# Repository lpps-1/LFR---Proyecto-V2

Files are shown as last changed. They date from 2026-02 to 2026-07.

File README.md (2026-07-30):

<div align="center">

[Linktree](https://linktr.ee/team.lpps1) | [GitHub](https://github.com/lpps-1) | **Status: Competition Ready**

</div>

---

## Team LPPS Overview

> **Team LPPS**, an elite youth-led competitive robotics and engineering collective based in Pakistan. Completely self-funded and operating independently with zero corporate or institutional backing, our core members peak at just 15 years old, yet we consistently dominate university-level national arenas, securing over 9 major championship titles. We are renowned for pushing the boundaries of indigenous hardware innovation, having pioneered Pakistan's first locally manufactured high-grip silicone wheels for competitive robotics. We are also currently working on Pakistan's first custom high-amp motor drivers and 16-channel sensors capable of a 1MHz sample rate, alongside advanced autonomous firmware architectures, custom onboard OLED control systems, and high-performance line-following robotics engineered for premier platforms such as the National Engineering Robotics Contest (NERC) at NUST EME.

### 1 - Introduction:
Hi! Line Follower Robot - Proyecto V2, is the second version of my line follower. The old one had some design flaws which I had solved in this design. So what I have made is a LFR with four TT motors for movement which will be paired with soft rubber tyre for extra traction as line followers need traction. Im using arduino nano for all the main processing, TB6612FNG as the motor driver for controlling the motors. What I have improved is that I have added a a 5 Channel TCRT5000 Array at the very front, which will be primarily detecting the line behind are two individual TCRT5000 Sensors on both sides that will be mainly used for detecting intersections and will also assist with turns. Two LEDs are also added that will turn on when the respective turn is being executed this will help in debugging and during a competition if the wrong LED turns on Ill know it will go off course and Ill be able to take the retry earlier instead of wasting time waiting for the robot to go off track. Lastly Im using a custom OS on the OLED which will show a starting animation which is also skippable then it will show multiple menu options. I have been working on it for about 4 months and its about to be completed but due to my upcoming final exams I have to delay it. The menu options will compromise of BLACK LINE, WHITE LINE, SENSOR CALIBRATION, MOTOR CALIBRATION, DIGITAL VALUES, and ANALOG VALUES. These modes will be selected through the installed four push buttons assigned as OKAY, CANCEL, UP and DOWN. My target is to make an OS which works like a programmer means during competition it will not leave the need of a laptop to change settings. All the threshold changes, sensor calibration and motor speed will be able to be changed using the buttons and the OS will make the robot more competitive and faster to edit the code instead of opening the laptop, going to the code file, changing the values and then finally uploading. 

### 2 - Reason for Making Proyecto:
Since 2020, I have been participating in national level events in Pakistan. At the start I used to participate at middle - high school competition but due to lack of competitiveness I moved towards university competitions. In which I have been victorious, I have won over 9+ national events University level last year alone. Due to being the only high schooler in the competitions the Unversity's directors had regarded and mentioned us too. They offered us different opportunities such as using their labs (tools not electronics) for creating our robot and for conducting team meetings. Regardless due to my interest in robotics I had been doing it and participating in competitions representing my school as well as my private robotics team. This robot is mainly for competition participation but after this robot Ill be moving towards encoders EDFs to provide enough down force allowing my robot to trace line even on the wall. This robot will be the most advance robot that I have worked on and after it Ill either make the EDF and encoder LFR afterwards or make a sumo robot afterwards. Either way Ill be making a sumo bot too. This robot will serve as the base for my future endeavors as Ill be doing different tests on it and will have to find a new a microcontroller faster, more pins and without any wifi or bt built in. Most probably tennesy 4.0.

### 3 - Usage:
Now lastly. How to operate Proyecto? Opearting Proyecto is very easy. First you will have to connect the battery connectors which will power up the circuit. After it the OLED will also lit up and start the animation with the robot name and the team name, if you want you can skip the animation by clicking the OKAY button. Once skipped or if the animation has completed the screen will show menu options through them you can scroll UP and DOWN through pressing the respective button and to select a function you will have to press OKAY then you will enter that mode, clicking OKAY will make the robot do the task (Sensor Readings, Line Following, etc). If you want to stop the robot from doing a specific task you can press the CANCEL button it will bring you back to the menu option. The robot can follow black line, white line and also can shift mid line tracing like after black line white lines starts it will adapt.

### 4 - Circuit Diagram:
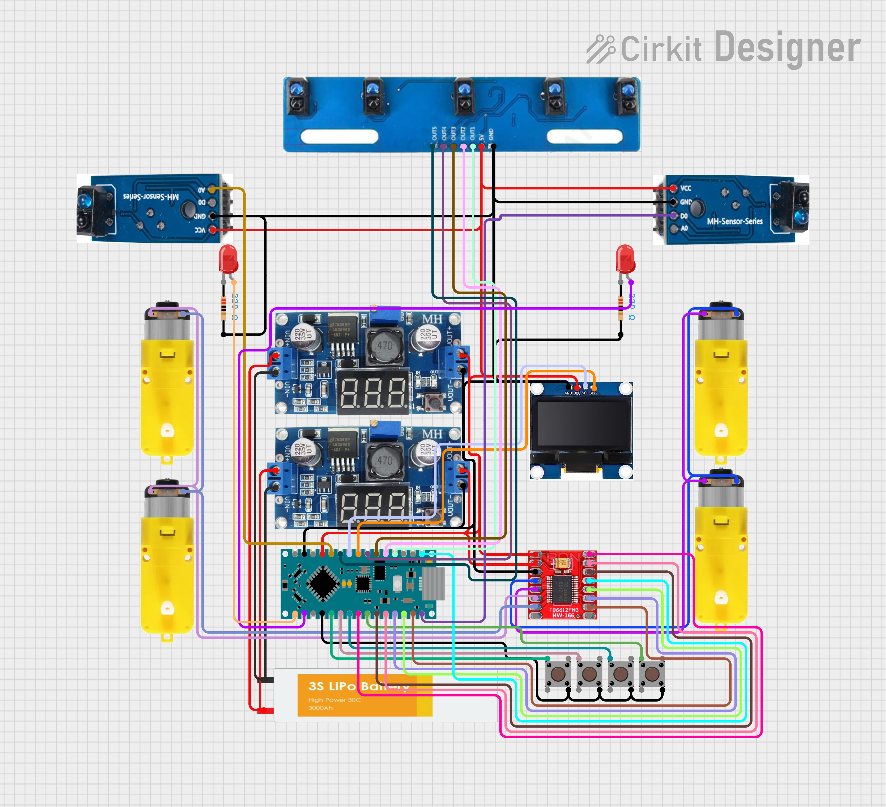
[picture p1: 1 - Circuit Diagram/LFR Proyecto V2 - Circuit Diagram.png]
Circuit Diagram


### 5 - 3D Model:

TinkerCAD Links:
* [Proyecto V2](https://www.tinkercad.com/things/l9xJPmTRQzA-proyecto-v2?sharecode=hnvhtCH3v41c5K6T4RtM-VqiNpLFxgLBMW4Wglu9lU8)
* [Proyecto V2 - Electronics](https://www.tinkercad.com/things/5jzzp9ZvHWP-proyecto-v2-electronics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)
  
<div align="center">
  <table border="0">
    <tr>
      <td align="center" colspan="2">
        <p><strong>Top View</strong></p>
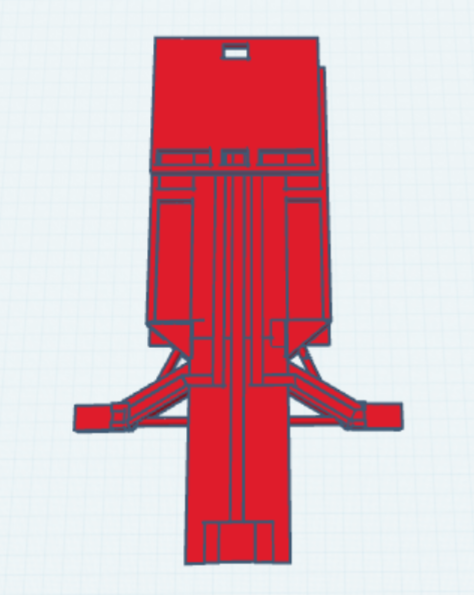
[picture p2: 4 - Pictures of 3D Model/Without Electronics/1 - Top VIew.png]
        
      </td>
    </tr>
    <tr>
      <td align="center">
        <p><strong>Left Side View</strong></p>
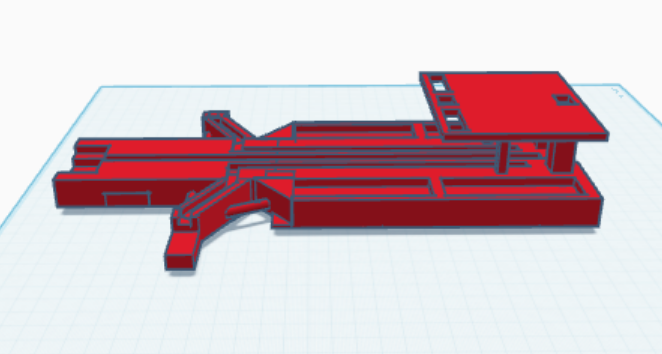
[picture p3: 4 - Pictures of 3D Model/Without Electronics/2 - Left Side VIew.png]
        
      </td>
      <td align="center">
        <p><strong>Right Side View</strong></p>
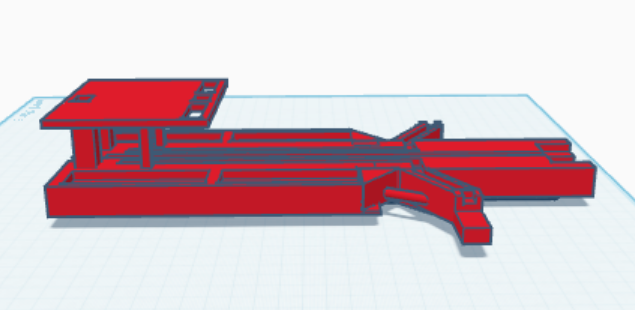
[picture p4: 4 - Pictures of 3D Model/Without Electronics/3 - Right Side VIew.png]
        
      </td>
    </tr>
    <tr>
      <td align="center" colspan="2">
        <p><strong>Back View</strong></p>
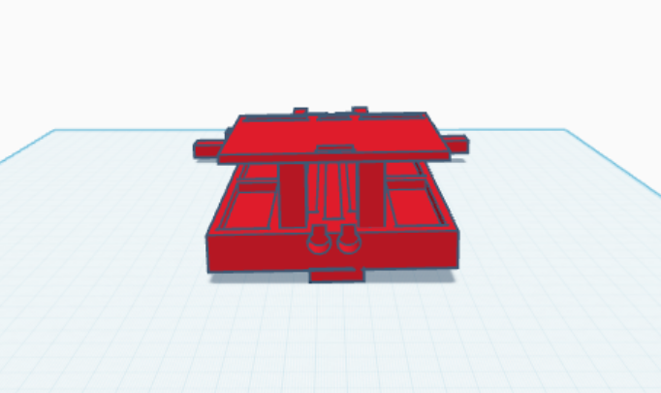
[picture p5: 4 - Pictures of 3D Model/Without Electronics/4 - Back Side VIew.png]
        
      </td>
    </tr>
  </table>
</div>

### 6 - Bill of Materials (BOM):
### Project Component List

| Name | Quantity | Total Price (USD) | Link |
| :--- | :--- | :--- | :--- |
| TB6612FNG Motor Driver | 5x | $5.74 | [aliexpress.com](https://www.aliexpress.com/item/1005010405309752.html) |
| Arduino Nano | 5x | $14.06 | [aliexpress.com](https://www.aliexpress.com/item/1005006725908213.html) |
| Oled Screen 1.3" | 4x | $7.24 | [aliexpress.com](https://www.aliexpress.com/item/1005008365029314.html) |
| Lipo 3s | 1x | $30.21 | [hobbylobby.com.pk](https://www.hobbylobby.com.pk/product/gen-ace-lipo-2200mah-3s-35c) |
| TCRT5000 5 Channel Array | 5x | $8.58 | [aliexpress.com](https://www.aliexpress.com/item/1005008733257121.html) |
| TCRT5000 Individual | 10x | $4.66 | [aliexpress.com](https://www.aliexpress.com/item/32866136486.html) |
| TT Motors | 4x | $9.72 | [aliexpress.com](https://www.aliexpress.com/item/1005006964177842.html) |
| Rubber Wheels Pair | 4x | $29.48 | [aliexpress.com](https://www.aliexpress.com/item/1005009333838697.html) |
| 6mm Hex Coupler | 4x | $7.36 | [aliexpress.com](https://www.aliexpress.com/item/1005009683741921.html) |
| Buck Convertor LM2956 | 5x | $6.52 | [aliexpress.com](https://www.aliexpress.com/item/1005010400036740.html) |
| Push Buttons | 1000x | $12.42 | [aliexpress.com](https://www.aliexpress.com/item/33029546857.html) |
| Perf Board | 1x | $10.55 | [aliexpress.com](https://www.aliexpress.com/item/1005007977139251.html) |
| Shrink Tube | 1x | $7.47 | [aliexpress.com](https://www.aliexpress.com/item/4000200124003.html) |
| Breadboard Hard Wires | 1x | $7.20 | [aliexpress.com](https://www.aliexpress.com/item/1005007079142852.html) |
| Male to Female Wires | 1x | $1.99 | [aliexpress.com](https://www.aliexpress.com/item/1005008070896908.html) |
| Male to Male Wires | 1x | $1.99 | [aliexpress.com](https://www.aliexpress.com/item/1005008070896908.html) |
| Female to Female Wires | 1x | $1.23 | [aliexpress.com](https://www.aliexpress.com/item/1005008070896908.html) |
| Female Header Pins | 1x | $1.99 | [aliexpress.com](https://www.aliexpress.com/item/1005010604381492.html) |
| Male Header Pins | 1x | $8.52 | [aliexpress.com](https://www.aliexpress.com/item/1005005509891182.html) |
| **Taxes** | - | $113.62 | N/A |
| **Shipping** | - | $9.69 | N/A |
| **Total Cost** | - | **$306.16** | N/A |

>

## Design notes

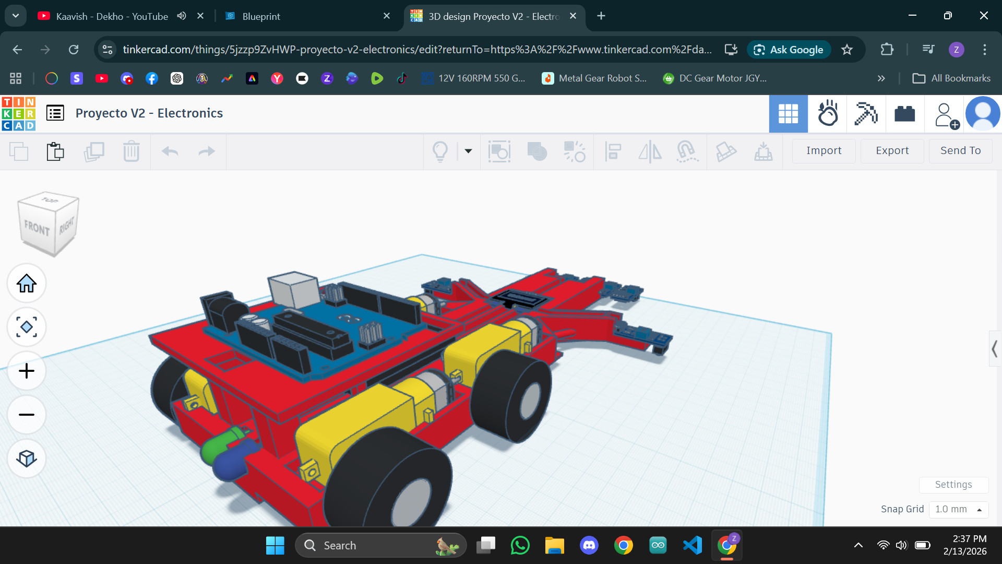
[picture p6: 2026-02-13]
4 - Pictures of 3D Model/With Electronics/4 - Back Side.png

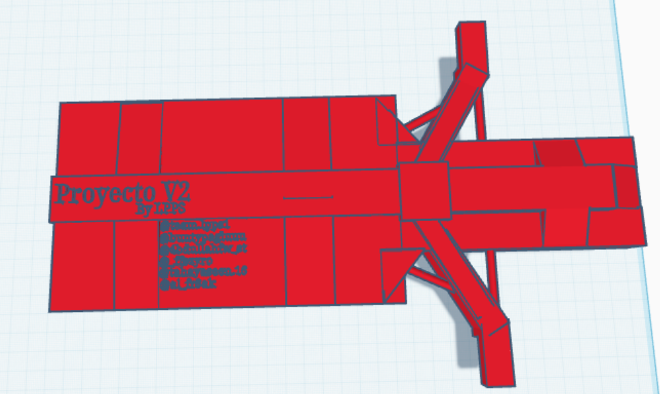
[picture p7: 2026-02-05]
4 - Pictures of 3D Model/Without Electronics/5 - Bottom VIew.png

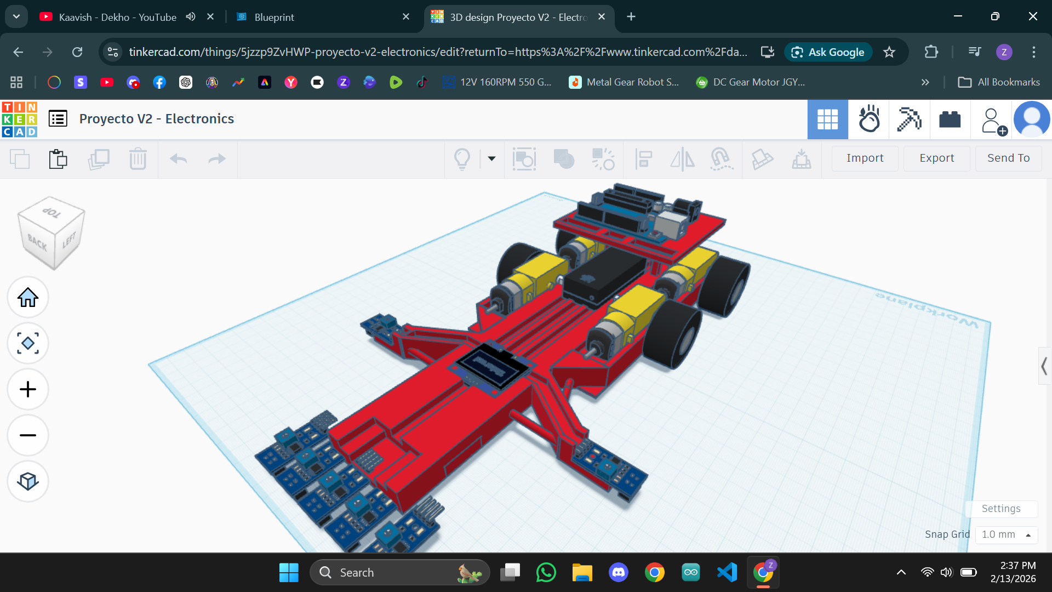
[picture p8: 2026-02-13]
4 - Pictures of 3D Model/With Electronics/2 - Right Side V2.png

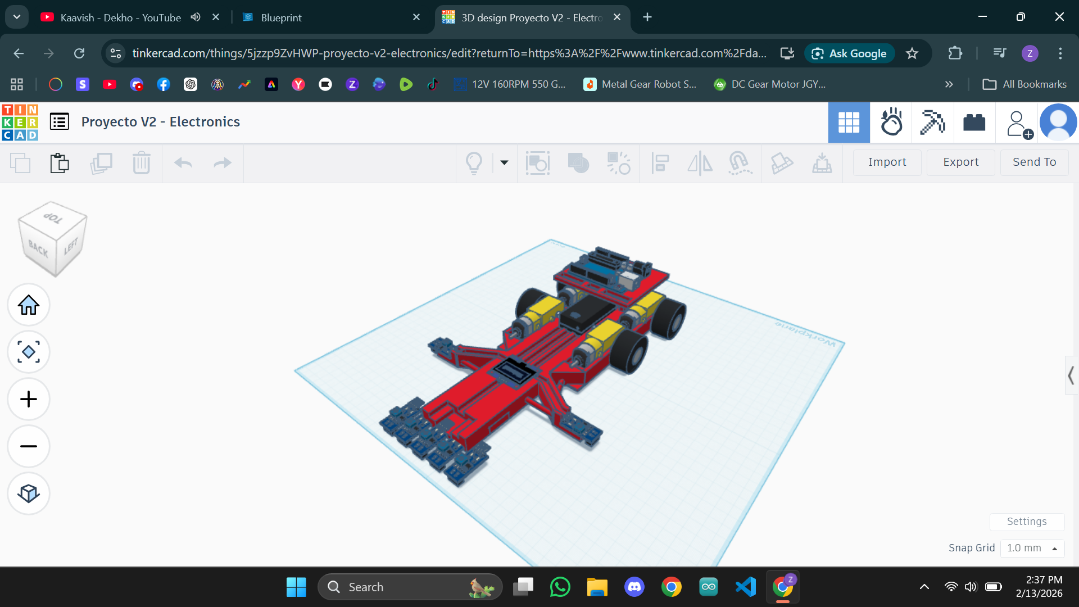
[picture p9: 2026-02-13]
4 - Pictures of 3D Model/With Electronics/1 - Right Side.png

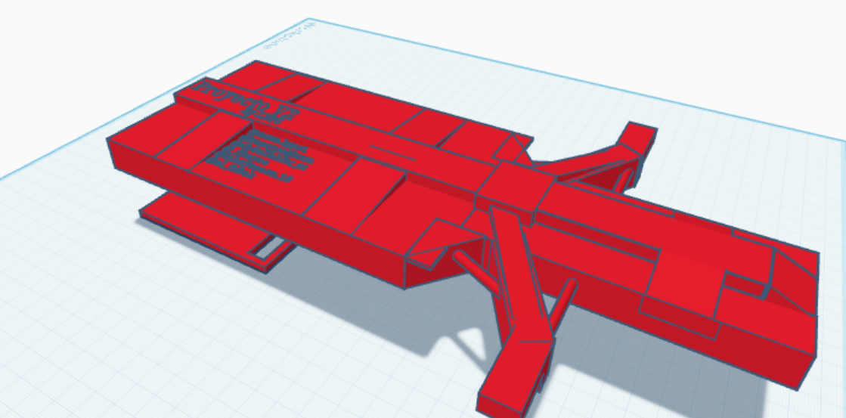
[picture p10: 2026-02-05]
4 - Pictures of 3D Model/Without Electronics/5 - Bottom View V2.png

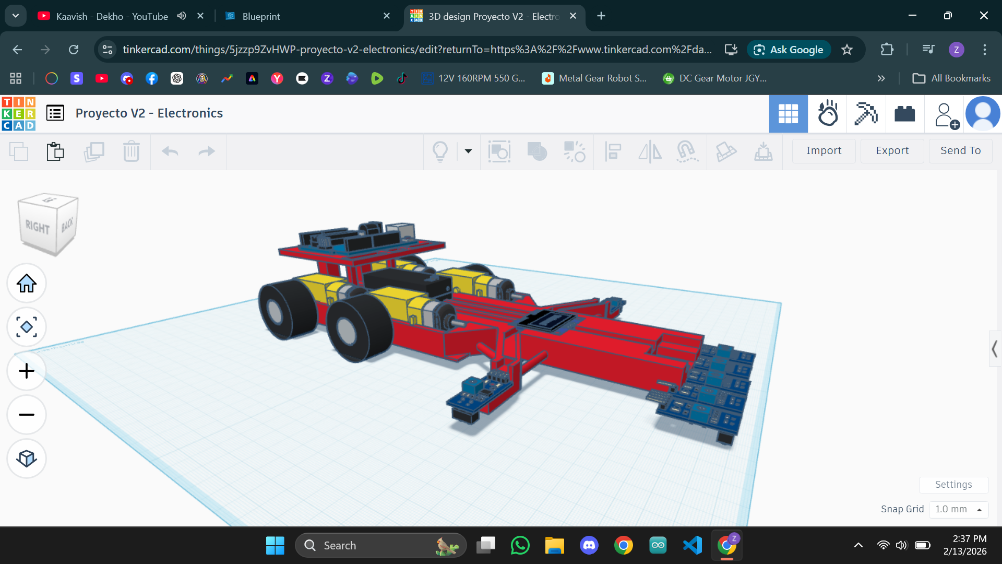
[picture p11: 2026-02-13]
4 - Pictures of 3D Model/With Electronics/3 - Left Side.png

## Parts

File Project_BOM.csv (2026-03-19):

Item | Cost | Source
TB6612FNG Motor Driver (5x) | 5.74 | https://www.aliexpress.com/item/1005010405309752.html?curPageLogUid=q2ncV5OVV5I6
Arduino Nano (5x) | 14.06 | https://www.aliexpress.com/item/1005006725908213.html?curPageLogUid=L5ovpbqzF0W0
Oled Screen 1.3" (4x) | 7.24 | https://www.aliexpress.com/item/1005008365029314.html?curPageLogUid=wgQPrdNYfJyg
Lipo 3s (1x) | 30.21 | https://www.hobbylobby.com.pk/product/gen-ace-lipo-2200mah-3s-35c
TCRT5000 5 Channel Array (5x) | 8.58 | https://www.aliexpress.com/item/1005008733257121.html?curPageLogUid=XYRuw7RoT89R
TCRT5000 Individual (10x) | 4.66 | https://www.aliexpress.com/item/32866136486.html?curPageLogUid=QIs360bCwifL
TT Motors (4x) | 9.72 | https://www.aliexpress.com/item/1005006964177842.html?curPageLogUid=7eC8UMwUJMGT
Rubber Wheels Pair (4x) | 29.48 | https://www.aliexpress.com/item/1005009333838697.html?curPageLogUid=SRXW20NJBT6p
6mm Hex Coupler (4x) | 7.36 | https://www.aliexpress.com/item/1005009683741921.html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
Buck Convertor LM2956 (5x) | 6.52 | https://www.aliexpress.com/item/1005010400036740.html?mp=1
Push Buttons (1000x) | 12.42 | https://www.aliexpress.com/item/33029546857.html?curPageLogUid=Apj7tqwX87d2
Perf Board (1x) | 10.55 | https://www.aliexpress.com/item/1005007977139251.html?curPageLogUid=D0iBHlUXi1K2
Shrink Tube (1x) | 7.47 | https://www.aliexpress.com/item/4000200124003.html?curPageLogUid=KCh5gYEvNmAw
Breadboard Hard Wires (1x) | 7.2 | https://www.aliexpress.com/item/1005007079142852.html?curPageLogUid=fxgxOiej1AmX
Male to Female Wires (1x) | 1.99 | https://www.aliexpress.com/item/1005008070896908.html?curPageLogUid=CrfvSCBDh73F
Male to Male Wires (1x) | 1.99 | https://www.aliexpress.com/item/1005008070896908.html?curPageLogUid=CrfvSCBDh73F
Female to Female Wires (1x) | 1.23 | https://www.aliexpress.com/item/1005008070896908.html?curPageLogUid=CrfvSCBDh73F
Female Header Pins (1x) | 1.99 | https://www.aliexpress.com/item/1005010604381492.html?curPageLogUid=JRoH24hlhWys
Male Header Pins (1x) | 8.52 | https://www.aliexpress.com/item/1005005509891182.html?curPageLogUid=7i6Brs3NDOU5
Taxes | 113.62 | N/A
Shipping | 9.69 | N/A
Total | 306.16 | N/A

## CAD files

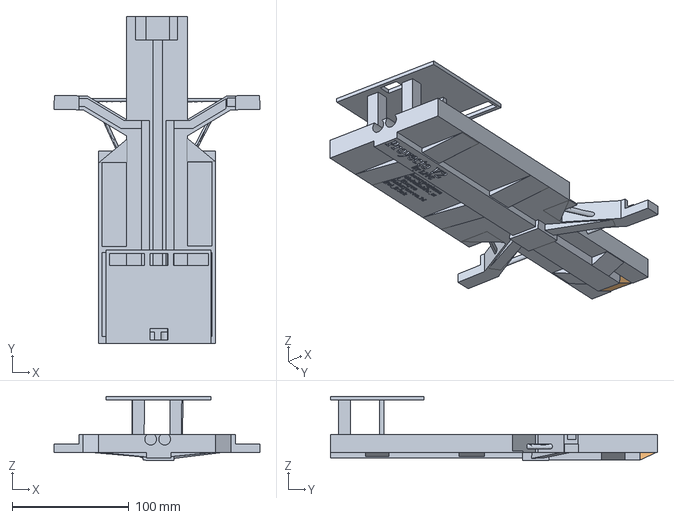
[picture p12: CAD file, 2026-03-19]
2 - 3D Model Files (STEP + F3d/Proyecto V2 .step
176.0 x 280.0 x 55.2 mm

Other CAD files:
2 - 3D Model Files (STEP + F3d/Proyecto V2 - Electronics .step
2 - 3D Model Files (STEP + F3d/Proyecto V2 - Electronics.f3d
2 - 3D Model Files (STEP + F3d/Proyecto V2.f3d

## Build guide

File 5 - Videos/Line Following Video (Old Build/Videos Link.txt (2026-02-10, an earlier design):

https://drive.google.com/drive/folders/1J60aQYIjLh-ZVWl0S96R7gH1Kvllh-a0?usp=sharing

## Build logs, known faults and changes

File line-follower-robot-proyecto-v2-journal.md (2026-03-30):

<!--
  This journal is auto generated by Hack Club Blueprint.
-->

# 2/4/2026 - Building the 3D Model  

_Time spent: 7.0h_  

### 1- Introduction:
I have prior experience in building line follower robots, I have made over 8-9 robots in total out of which 4 line followers, two RC cars, one sumo robot and one being a 5kg robowar category robot. I mainly specialize in line followers and have won many national level events. In Pakistan I used to participate at high school level but due to lack of competition I moved towards University categories. In which Im victorious till now and the university directors especially mention and regards me for participating. Now lets move towards my design.

So basically this is a version 2 of the original one that i made on perf boards, like I used it as the base as well as the circuit and with two TT gear motors. The gap between the main board and the sensor was like 25 inches which wasnt a good idea due to which it had to be put on my display shelve. But from that design I learnt a lot and improved a lot which I have applied in this design.

Screenshot (287)

### 2- Design Breakdown:
So in this design what I have done is that basically, Im using four TT motors one after another. Im using two on each side each because with two the turning becomes very smooth which is what I need in my line follower. At the very front I will be using a TCRT5000 5 channel array. Even though its basic but to be honest I have used Polulu QTR8A Reflectance Analog Sensors but these cheap digital sensor works better which is evident through the performance in the robotics events that I had participated in. The robot main body has engravings which are the paths for the jumper wire to keep the build clean looking. I have also added a parallel block like you can see before the sensor position there is a straight line type part on which Ill put a TCRT5000 individual sensor on each side. These will be used for detecting cross sections. As in the upcoming event which is one of the biggest robotics event in Pakistan (NERC 26), there track comprises of intersection, through which you have to take a specific path. But this robot is for overall general purposes and intersections are usually added in a track to confuse the bot. To support these parallel blocks for sensor I have added diagonal support for both the performance reason as well as aesthetic reasons. 
Now moving towards the suspended platform. It will have the main PCB which Ill be making through perf board instead of the usually printed one. On the board will have an arduino nano for processing, TB6612FNG as the motor driver, 4 Push buttons, some female headers to easily connect a HC-05 to make the robot RC if needed. Ill also connect an OLED Screen which will run my custom OS. Which I have been designing for 3-4 months. Lastly the model has two semi circled cut which will have two different color LEDs. What they will do is that for example the left side LED is Green colored while the left side will be Blue. Now according to the robot logic Ill add that, if robot is taking a right turn it should turn on the Green LED and when taking left it will turn on the Blue LED. This helps a lot with debugging as sometimes robot takes the opposite turn even though the track conditions are for the different turn. It will be used for debugging purposes and during competition if the wrong LED turns on Ill know to take a retry instead of waiting for the robot to go off course saving crucial time. Ill upload another photo below which will explain the each part location.

Sensor Array (1)

### 3- OLED System:
So here I have clearly marked the model's parts with it's uses. Another thing that I forgot to mention was the OLED position which I have shown here the button will be on the main PCB. As there will be four buttons. OKAY, CANCEL, UP, and DOWN the screen will start with an animation showing the robot name and my team name. The animation will be skipable as during the competition a retry doesnt has that much time. After the animation it will show multiple options such as Black Line, White Line, Sensor Reading Analog, Sensor Reading Digital, Motor Calibration, Sensor Calibration, and finally LED Calibration. The alleviated platform for the PCB has holes for the jumper wires connecting the electronics to the main board. Now Ill upload the side angles photos and back angle photos. Then Ill move to the under side of the robot. Ill label the next photos at the top so it is easier to understand.

### 4- Photos from Various Angles:
Sensor Array

Sensor Array (1)

Sensor Array

### 5- Reinforcement at the Bottom:
Now as you have seen as well as read about the side angles, top, front and back angles. The last part is the bottom part which has the additional support as well as my robotics team's instagram ID and the robot'ss name engraving. I have added the support in the bottom as the heavy parts such as the motors are at the corners of the structure and with the wheels it will create a bend in the middle. To counter that I have used the strongest geometrical shape which divides the force on all side triangles. I have added a straight beam with multiple triangles subtending from it. This helps with keeping the structure durable and firm. Allowing it to last longer and being able to handle more wear and tear. Let me add a picture below which will clear your doubt further.

Sensor Array (1)

# 2/5/2026 10 AM - Circuit Diagram   

_Time spent: 5.6h_  

### 1- Introduction:
So today I worked on the circuit design. As I had already mentioned this is my 4th LFR, so I pretty much used the same pinout. But due to having a lot of components Im using all the pins of it both analog and digital one. For LEDs I had to even use the D0 and D1. As these pins are directly hard wired with the ATMega chip, if the LEDs are left connected while uploading code or during serial debugging tasks it will fail. As the LEDs will interfere with the ground state of these serial pins. To counter this Ill make the LEDs removeable so when I need to upload/serial debug Ill just have to remove the LEDs. This will be a hassle at the start as Ill be needing to change values and calibrate the robot. But once calibrated it won't be a big of an issue. Now let me upload the circuit design then Ill start explaining what and why I did such a wiring.

circuit_image (1)

### 2- Component List:
Yes, I know you'll be confused at the schematics but before explaining it. Let me breakdown what I have used and a brief reason for using it.

**i) Arduino Nano 1x -** Easy to source, and best for this task.

**ii) TCRT5000 5 Channel Array 1x -** Works best for me, as I have tested both the Pololu QTR8A and these in competitions.

**iii) TCRT5000 Individual Sensors 2x -** For detecting cross sections, assist with turns.

**iv) 3S 12.6V Lipo 1x -** LIPOs for its high discharge, 2200mAh as Im using four motors that will drain anything less than 1000mAh easily.

**v) LM2596 Buck Convertor 2x -** What I learnt from my previous build was that, I was powering the VCC (Logic Voltage to be 5v of TB6612FNG) form the nano directly. The nano's linear voltage regulator had been fried which I wasn't aware of. Due to which instead of giving 5V at the 5V pin. Nano was giving out 8V which made around 3-4 TB6612FNG explode as I couldn't find the problem. To tackle this Im using two bucks one for 12v to feed into TB and one moderated for 5v for Nano and TB's VCC. By using a buck on TB's VM it helps me by keeping the same RPM as you know Im not using encoders if the battery voltage drops the same value which was set 255 wont be the same at 8V. It will be definitely slower to tackle this and keep a consistent voltage Im using a second buck.

**vi) TT Motors 4x -** For movement and four for smoother turning.

**vii) OLED 1x -** Will be used to operate my custom OS which I have been working on for over 4 months and is almost complete. It will have multiple menu options which can be selected through the four push buttons which I have used.

**viii) Push Buttons 4x -** For the selection of menu options. OKAY, CANCEL, UP and DOWN they will be assigned these functions. I have connected each 4-Pin push button to only GND and a signal pin not connecting it to 5V to reduce wiring as it can be operated by using the internal pull up function in the code.

**ix) TB6612FNG 1x -** Motor driver for controlling the motors. I have chosen it as it transfers electricity to motors with the efficiency of about 70 - 80% unlike l298n which wastes lots of voltage as heat.

**x) LEDs 2x -** Lastly two LEDs, for debugging purposes, as they will turn on depending on the robots decision of turning. This will help me in debugging and also during competition it will tell me that the robot will go off course without me having to wait for it to go off course. Saving crucial time and allowing me to put it back on the track quickly.

### 3- Explanation: 
So, I think most of your questions will be cleared about the component selection. The thing that took me the longest was to find two pins for the LEDs but unfortunately I had already used all of them. But I found a solution that I can plug them to D0 and D1 although these are directly connected to the ATMega and are responsible for uploading of the code as well as serial monitor reading. So when I'll need to upload the code or serial read I'll have to remove the LEDs or the code wont upload. As the LED interferes with the serial signals ground state and causes voltage spikes. This issue will be painful only during the assembly as once the robot is calibrated I won't be required to remove them and as for the speed setting I'll use the push buttons. What I want is that to make a mobile type application software meaning during competition if I want to change some setting I dont have to use my laptop to change speeds, calibration, threshold, etc. By making the OS all of these will be done through the four push buttons Im using like changing the speed, Ill make a counter which increases with each press and then once clicked saved the setting is changed in the code means changing the PWM value of motors. Same logic will be applied for checking sensor assignments and threshold changes. What I have planned is to add a single 3" by 3" server fan. Which I already have its very strong and very good with cooling which I had used in my old build too. As during calibration repeated use of the motors and the region (Pakistan, Lahore. In summer it gets up to 48C Degrees) where I live TT motors get hot.   

# 2/5/2026 2 PM - Downloaded the FreeCAD  

_Time spent: 3.0h_  

Now to apply for project design, there is a requirement of uploading a STEP file but I used TinkerCAD for designing due to which, Ill first have to download freeCAD then convert the STL file into STEP through it. Along with that Im making the github repository. In which Im done with uploading the READMe and screen shot of the 3D model. Now Im working on making the 3D model file into STEP and after that Ill use the freeCAD for adding electronics to my design as it is also a requirement for applying.

Screenshot (294)

# 2/6/2026 - Converted my STL file into STEP file  

_Time spent: 3.0h_  

As I used tinkerCAD for designing my 3D model, due to which it was in STL. and OBJ. only while the guidelines for project submission is to have a STEP file. The main difference is that the STL and OBJ only consist of triangles while STEP allows more complex geometric shapes and it was also evident as the STL file was only 3MB while the STEP file was 177MB. It took me more than two hours to convert the STL file into STEP. Then finally I found a YouTube tutorial which guided me how to do it. I tried with AutoDesk Fusion but it didnt work then I downloaded FreeCAD and it finally worked. Along with this I took multiple screenshot of the model and organized them. This took me about three hours as the STEP file was over 25MB it wasnt able to be uploaded directly as the max allowed from the website was only 25MB and from the gitBASH it only allows 100MB max. Due to this I used Google Drive to externally save the file and gave the link in a text document. 

Screenshot (295)

# 2/9/2026 7:11 AM - The Coding Part V1  

_Time spent: 0.5h_  

### 1) Introduction:
Now Ill be talking about the coding part. I have divided the coding files into these parts.
 - Motor Test
 - Sensor Position Test
 - LFR Code
 - LFR Code Combined with the OLED and Animations
 
Each of these will be consider as a part for example, Part V1 will be talking about motor test.

### 2) Code Explanation:
The code starts with the importing of the SparkFun_TB6612FNG library which you'll have to download from the browser you use or from github. Using this library shortens the code as without it you have to code like this:

**Without the library**
   Void Forward() {
     AIN1(digitalWrite, HIGH);
     AIN2(digitalWrite, LOW);
     PWMA(AnalogWrite, 255);
     BIN1(digitalWrite, HIGH);
     BIN2(digitalWrite, LOW);
     PWMB(AnalogWrite, 255);

This makes the code larger and a bit complex on the other hand using the sparkfun library this code can be easily written like this only in two lines!

**With the library**
Motor motorA(AIN1, AIN2, PWMA, 1, STBY);
Motor motorB(BIN1, BIN2, PWMB, 1, STBY);

   Void Backward() {
    motorA.drive(255);
    motorB.drive(-255);

The only difference is that you will have to define two integers at the top such as motorA and motorB after it you can just tell the motor to driver and the numerical value in the brackets tell the speed and if negative sign is added to the numerical value it makes the tyre spin backward. So now you may be wondering what this could does. By using this could you can check the motor directions as you know we are using TB6612FNG which officially supports two motors but if we common the wires of the two motors on each side we can use four motors and this works with more motors too, but depends on their current draw and voltages. This could makes the motor move forward for few second, then backward, then left and finally right. As we dont have the traditional steering system we make the robot turn by the following method. Consider if we want the motor to take the left turn we can do it by the following code

leftmotor.drive(-200);
rightmotor.drive(200);

To take a turn we will have to make the same side of motors go in reverse as the turn. If we want a right turn we will make the the right side go reverse while left one go forward.

Screenshot (296)

# 2/9/2026 7:22 AM - The Coding Part V2  

_Time spent: 0.8h_  

### 1- Introduction:
Now we will be talking about the Sensor Position Testing Code. In my line following code Im using a list like:
static int sensorPins[NUM_SENSORS] = {A6, A3, A2, A1, A0};
By using a list I can directly assign there respective thresholds as well. During line following as I have already told Im using the if-else logic instead of the PID one. The middle of the list is declared as C (center) then the right side from C meaning A1 and A0 as R1 and R2. R1 helps with slight turns meaning the correction on the line while R2 guides with the turn detection as well as the execution of the turns. A3 and A6 are L1 and L2 respectively, same logic is applied to them as well. The line following code main goal is the always keep the C on the line by using the left side and right side readings it helps with correction and turns. Making the robot follow the black line.

### 2- Explanation:
Now I will be moving towards the coding part, in this code nothing happens only the serial read and this code's sole purpose is to check if the sensors are correctly assign meaning it shouldnt be like that the C is printed on the serial monitor while R2 is on the line. The code helps with checking if the wires are correctly connected if not then we can fix it through software instead of changing the wiring. This makes it much easier as if the line following code is directly ran, it will behave weirdly and using the line following code to check the sensor assignment will be very hard and difficult and wont be efficient for this task. I have written the code beforehand and all the coding has been tested on my old LFRs, but I do have made some changes in the code for my new LFR Proyecto V2.

Screenshot (297)

# 2/10/2026 1:03 PM - GitHub Profile Building V2  

_Time spent: 0.5h_  

Just got done with uploading the videos of my previous LFR showing the current line following logic which Im using in this build too with some changes, along with the custom OS videos showing the menu function working and user interface. You can see the videos your self too.

Custom OS: https://drive.google.com/drive/folders/1uGLSIxmfm0eLZAYhKWAmIYZnSm4inEtt?usp=drive_link
Line Following: https://drive.google.com/drive/folders/1J60aQYIjLh-ZVWl0S96R7gH1Kvllh-a0?usp=sharing

Screenshot (305)

# 2/10/2026 1:48 PM - GitHub Profile Building V3  

_Time spent: 0.5h_  

Just got done with creating the BOM is csv style, uploading the files and other things. Added the circuit diagram in the readme as well as the BOM and the 3D design screenshots. The only part left now is the new custom OS video and everything is done.

Screenshot (306)

# 2/13/2026 4 AM - CAD with Electronics  

_Time spent: 2.0h_  

I had already made the 3D design. But the requirement of submissions narrates that the CAD file should have all of the electronics in the file. As I didnt have access to autofusion I used TinkerCAD for this task. Now Ill be converting this STL file into STEP using freeCAD

Screenshot (307)
Screenshot (310)Screenshot (308)Screenshot (309)

# 2/13/2026 5 AM - GitHub Profile Building V4  

_Time spent: 0.5h_  

Just got done with organizing the images of the 3D model. Made two folders one with my basic model and the other one with electronics on. Uploaded the STEP files using google drive as they are 400MB+. Direct upload wasn't possible. Now Ill be working on the OS to show the animation and skipping everything that I had programmed.
Screenshot (312)

# 2/14/2026 - GitHub Profile Building V5  

_Time spent: 0.3h_  

Today I made the last changes to my github before the submission. As the submission requires screen shots of the add to cart price. I was changing the the BOM as I had forgot to add the shipping and handling. Also battery was not being imported to Pakistan so I had to see some local batteries now the list is fully updated.



# 3/19/2026 - Changing Vendor  

_Time spent: 7.0h_  

I got a response from the team and they said that i shouldnt use amazon. So i first scavenged all the parts on aliexpress first. Secondly my CADs were not complete. I spent 3-4h and fixing the CAD file issues and around 3h on aliexpress.Screenshot (339)
Screenshot (345)Screenshot (344)Screenshot (340)
Screenshot (346)Screenshot (343)

# 3/30/2026 9:52 AM - The Coding Part V3  

_Time spent: 7.0h_  

### 1) Introduction:
Today Ill be talking about the line following logic. Instead of PID  I have adopted a unique if-else logic. Ill explain below.    -
3 - Left Side

# 3/30/2026 9:53 AM - The Coding Part V4  

_Time spent: 7.0h_  

### 2) Explanation:
Most LFR take turns according to the current situation like if the R1, R2 and maybe C is on the line it initiates the right turn. This logic is more reactive but sometimes there are T sections on which this logic is completely useless as the robot gets stuck in a loop. To tackle this the code Im using initiates the turn after all the sensor gets off the line then it checks the integer last seen. What last seen does is that it check which sensors were low before all sensors got high. If R1, R2 and maybe C were low before getting high the robot will know its a right turn and it will spin clockwise until C is back on the line. Same logic is used on the line tracing but last seen isnt used as much but it helps in a rare situation. As you know we cant achieve perfect wheel alignment and due to macro level differences in motors, each motor spins at a different RPM which makes the robot go in one direction slightly when moving forward. As the turn is very slow sometimes C was low and out of no where all the sensor gets HIGH the scenario happens that the C sensor and either R1 or L1 are just next to the line but they dont give any reading, confusing the bot. To tackle this I have added for the first time like after running if this happens robot wont have any previous data regarding last seen, so it just turns clockwise until any of the robot's sensor gets on the line then it corrects it self. If the situation occurs later on the robot is able to correct it self based on the previous saved last seen. In this code the calibration and threshold is already defined which can be changed by using the sensor assignment / sensor reading code to find the threshold of each sensor. Lastly if I want to follow a white line Ill inverse the > signs which will make the robot trace inversely. I have perfected this code logic manually by testing on my previous robot. It took about 15H to 16H as I have to test each change manually on the robot and perfect the values and logic. This code works like a charm, Ill try to upload the videos of this code working on my old robot.

Screenshot (298)

# 3/30/2026 9:54 AM - The Coding Part V5  

_Time spent: 7.0h_  

### 1) Introduction:
This is the main code which runs the LFR code as well as my custom OS. Ill explain the code in the following method:
  - main_.ino
  - menu.h
  - animation.h
  - logo.h
  - rc_mode.h
  - black_line.h
  - white_line.h
As you can see I have divided the code into tabs which I can call in the main file like libraries making the code more manageable and easy to modify.

### 2) main_.ino:
This is the main file which calls all the tabs in which distinct code is written. It handles all the loops as well as the button input. It allows the code to run and from here I can mainly change what the code do. If I want to disable a function Ill just have to remove the import at the top. It also mainly handle the button menu as buttons will be running forever so they need to be described here.

Screenshot (299)

### 3) menu.h:
Now this file contains all the menu options like the ones I talked about earlier (sensor calibration, digital values, etc). This file has all the menu options and also describes them. Some of few which are larger for example like black.h and white.h they are not directly defined in this file as it will make the code longer. Only shorter parts like motor test, calibration, etc are described here. Through this file we can add/remove any function as well as we can edit it. It also deals with the scrolling mechanism as well as entering/existing and finally the animation skipping part.

Screenshot (300)  

# 3/30/2026 9:55 AM - The Coding Part V6  

_Time spent: 7.0h_  

### 4) animation.h:
This file deals with the starting animation which first shows the logo of my team (LPPS) it shows the logo as well as the name of my team. Then it shows the name of the robot model and version of the robot. This animation lasts about 4-5 secs. This is added solely for aesthetics due to which it is skippable as during competition you dont have enough time to wait for the boot up screen.

Screenshot (301)

### 5) logo.h:
As you know to show an image on the OLED you first have to convert into a bitmap which can be done by using online free softwares. I was using a colored image first to be converted into bitmap the code went over 16k+ lines due to which I had to downsize the logo as well as convert it into a black and white image. After doing that it is still 100+ lines. The logo is directly imported from here to the animation file.

Screenshot (302)

### 6) rc_mode.h:
This mode is under development which I have been testing. When this option is selected the screen shows ready to pair then once a specific character is sent form the connected device it shows the device name and says connected to blah blah. To be able to use the rc_mode you have to connect a HC-05 without it wont work. It uses the serial.bt and use the character communication for controlling the motors.

Screenshot (303)

# 3/30/2026 9:55 AM - The Coding Part V7  

_Time spent: 3.0h_  

### 7) black_line.h:
This file contains the actual line following code which I explained in the earlier journal. I have made the line following code a different file so it is easier to change the values of the motor PWM and sensor thresholds. 

Screenshot (304)

### 8) white_line.h:
It will have the inverse following which I had also explained in the previous journal. This code file isnt made yet which will also be added in future as only the signs have to be changed to make it follow white line.

### 9) Other Modes:
Now lastly the calibration and reading modes. As I had mentioned before my final exams are near so I had stopped working on my OS which I will complete after my exams and it is nearly finish as you can see. Ill upload the videos of the animation screen and OS function on the github make sure to see them its pretty cool ig. As this had to be done manually each change had to be checked on the display and I had to also make sure no other modes are affected this took the longest. I had been working on this OS for over 3-4 months now. As this is general code like it will be used in my other projects so I will add the average time to setup the code for each build.

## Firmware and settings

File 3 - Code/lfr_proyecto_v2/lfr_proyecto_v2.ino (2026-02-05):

#include <SparkFun_TB6612.h>

#define NUM_SENSORS 5

// -------------------- SENSOR PINS --------------------
int sensorPins[NUM_SENSORS] = {A3, A1, A0, A6, A2};

// -------------------- MANUAL CALIBRATION VALUES --------------------
int whiteValues[NUM_SENSORS] = {974, 974, 973, 974, 974};
int blackValues[NUM_SENSORS] = {346, 345, 345, 345, 343};

int threshold[NUM_SENSORS];

// -------------------- MOTOR PINS --------------------
#define AIN1 7
#define AIN2 8
#define PWMA 5
#define BIN1 9
#define BIN2 10
#define PWMB 11
#define STBY 12

Motor motorA(AIN1, AIN2, PWMA, -1, STBY);
Motor motorB(BIN1, BIN2, PWMB, -1, STBY);

// -------------------- SPEED SETTINGS --------------------
int fullSpeed     = 240;
int turnSpeed     = 160;   // BASE correction
int hardTurnSpeed = 190;  

int motorDirection = -1;

// -------------------- LINE MEMORY --------------------
enum LastSeen { LEFT, RIGHT, NONE };
LastSeen lastOnTrack = NONE;

// -------------------- START BUTTON --------------------
#define START_BTN 6

// -------------------- THRESHOLD CALC --------------------
void calculateThresholds() {
  for (int i = 0; i < NUM_SENSORS; i++) {
    threshold[i] = (whiteValues[i] + blackValues[i]) / 2;
  }
}

// -------------------- SETUP --------------------
void setup() {
  pinMode(START_BTN, INPUT_PULLUP);
  Serial.begin(9600);
  calculateThresholds();
}

// -------------------- LOOP --------------------
void loop() {
  if (digitalRead(START_BTN) == LOW) {
    delay(50);
    if (digitalRead(START_BTN) == LOW) followLine();
  }
}

// -------------------- LINE FOLLOW --------------------
void followLine() {
  while (true) {

    int s[NUM_SENSORS];
    for (int i = 0; i < NUM_SENSORS; i++) {
      s[i] = analogRead(sensorPins[i]);
    }

    bool L2 = s[0] < threshold[0];
    bool L1 = s[1] < threshold[1];
    bool C  = s[2] < threshold[2];
    bool R1 = s[3] < threshold[3];
    bool R2 = s[4] < threshold[4];

    bool any = L2 || L1 || C || R1 || R2;

    if (any) {

      // ---------- PERFECT CENTER ----------
      if (C) {
        moveForward(fullSpeed);

        if (L1 || L2) lastOnTrack = LEFT;
        else if (R1 || R2) lastOnTrack = RIGHT;
      }

      // ---------- LEFT SIDE ----------
      else if (L1) {
        turnLeft(turnSpeed);          // SLIGHT correction
        lastOnTrack = LEFT;
      }
      else if (L2) {
        turnLeft(turnSpeed + 40);     // HARDER correction
        lastOnTrack = LEFT;
      }

      // ---------- RIGHT SIDE ----------
      else if (R1) {
        turnRight(turnSpeed);
        lastOnTrack = RIGHT;
      }
      else if (R2) {
        turnRight(turnSpeed + 40);
        lastOnTrack = RIGHT;
      }
    }

    // ---------- COMPLETELY LOST ----------
    else {
      if (lastOnTrack == LEFT)  spinAntiClockwise(hardTurnSpeed);
      else                      spinClockwise(hardTurnSpeed);
    }

    delay(2);
  }
}

// -------------------- MOTOR WRAPPERS --------------------
void moveForward(int speed) {
  motorA.drive(speed * motorDirection);
  motorB.drive(speed * motorDirection);
}

// SLIGHT turn = only 25% speed reduction
void turnLeft(int speed) {
  motorA.drive(-speed * motorDirection);
  motorB.drive(speed * motorDirection);
}

void turnRight(int speed) {
  motorA.drive(speed * motorDirection);
  motorB.drive(-speed * motorDirection);
}

void spinAntiClockwise(int speed) {
  motorA.drive(-speed * motorDirection);
  motorB.drive((speed *1/2) * motorDirection);
}

void spinClockwise(int speed) {
  motorA.drive((speed *1/2) * motorDirection);
  motorB.drive(-speed * motorDirection);
}
  

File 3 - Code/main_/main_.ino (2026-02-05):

#include <Wire.h>
#include <Adafruit_GFX.h>
#include <Adafruit_SSD1306.h>

#include "animation.h"
#include "menu.h"
#include "black_line.h"

#define SCREEN_WIDTH 128
#define SCREEN_HEIGHT 64
#define OLED_RESET -1

// Button pins
const int BTN_DOWN   = 2;
const int BTN_UP     = 4;
const int BTN_OK     = 6;
const int BTN_CANCEL = 3;

Adafruit_SSD1306 display(SCREEN_WIDTH, SCREEN_HEIGHT, &Wire, OLED_RESET);

// --- Button states ---
bool okPrev = HIGH;
bool cancelPrev = HIGH;
unsigned long lastCancelTime = 0;
const unsigned long cancelDelay = 500; // 500ms debounce

// --- Black line menu state ---
enum BlackLineState { MENU, READY_SCREEN, FOLLOWING };
BlackLineState blackLineState = MENU;

void setup() {
    pinMode(BTN_DOWN, INPUT_PULLUP);
    pinMode(BTN_UP, INPUT_PULLUP);
    pinMode(BTN_OK, INPUT_PULLUP);
    pinMode(BTN_CANCEL, INPUT_PULLUP);

    display.begin(SSD1306_SWITCHCAPVCC, 0x3C);
    display.clearDisplay();
    Serial.begin(9600);

    initBlackLine();

    // --- Startup animations ---
    bool skipAll = false;
    int logoW = 128, logoH = 128;
    float startScale = 0.2, endScale = 0.6, step = 0.04;
    int totalFrames = (endScale - startScale) / step;
    unsigned long frameTime = LOGO_ANIMATION_TIME / totalFrames;
    unsigned long lastFrame = millis();
    float scale = startScale;

    while (scale <= endScale && !skipAll) {
        display.clearDisplay();
        drawScaledBitmapCentered(teamLogoBitmap, logoW, logoH, scale, SSD1306_WHITE);
        display.display();
        if (digitalRead(BTN_OK) == LOW) skipAll = true;
        if (millis() - lastFrame >= frameTime) { scale += step; lastFrame = millis(); }
    }

    unsigned long glitchStart = millis();
    while (!skipAll && millis() - glitchStart < GLITCH_TIME) {
        glitchEffect(1);
        if (digitalRead(BTN_OK) == LOW) skipAll = true;
    }

    unsigned long nuevoStart = millis();
    while (!skipAll && millis() - nuevoStart < NUEVO_DISPLAY_TIME) {
        showNuevo();
        if (digitalRead(BTN_OK) == LOW) skipAll = true;
    }

    showOptions();
}

void loop() {
    bool okNow = digitalRead(BTN_OK);
    bool cancelNow = digitalRead(BTN_CANCEL);
    unsigned long now = millis();

    // --- CANCEL handling with 500ms ignore window ---
    if (cancelPrev == HIGH && cancelNow == LOW) {
        if (now - lastCancelTime > cancelDelay) {
            if (blackLineState == FOLLOWING) {
                stopBlackLine();
            }
            blackLineState = MENU;
            showOptions();
            lastCancelTime = now;
        }
    }
    cancelPrev = cancelNow;

    switch (blackLineState) {
        case MENU:
            handleMenuInput();
            renderMenu();

            // Check if Black Line is selected
            if (okPrev == HIGH && okNow == LOW) {
                String selected = menuItems[selectedIndex];
                if (selected == "Black Line") {
                    blackLineState = READY_SCREEN;
                    display.clearDisplay();
                    display.setTextSize(1);
                    display.setTextColor(SSD1306_WHITE);
                    display.setCursor(0, 28);
                    display.println("Press OK to Start Following");
                    display.display();
                }
            }
            break;

        case READY_SCREEN:
            // Wait for second OK press to start following
            if (okPrev == HIGH && okNow == LOW) {
                blackLineState = FOLLOWING;
                blackLineStopped = false;
                blackLineActive = true;
            }
            break;

        case FOLLOWING:
            if (blackLineActive && !blackLineStopped) {
                blackLineStep();
            }
            break;
    }

    okPrev = okNow;

    delay(20);
}
